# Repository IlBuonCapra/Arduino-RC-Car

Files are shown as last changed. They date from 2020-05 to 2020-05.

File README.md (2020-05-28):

# Arduino - RC Car
Arduino RC Car with nRF20L01 module, controlled by Syma X5C remote controller.
I used [Symaxrx Library](https://github.com/Suxsem/symaxrx) to control the car.

## PCB

I also created my personal shield for this projects using Eagle PCB.
Everything works with 12 volts from a battery packs made of six 18650 batteries.

A L298 Dual Full Bridge Driver is used to drive motors in each directions.
L298's enables are connected to 5 volts, so the motors are always ready to work.
If you want, you can short-circuit resistors R1,R2.
Unfortunaly, the steering motor is not controlled with PWM due to the reduced number of PWM pins of Arduino, but the car steers well.

12 volts leds are used like lights and a buzzer is used like clacson.

For this shield, i used the following pins:
| PIN | Function |
| --- | --- |
| 3 | CLACSON |
| 4 | LIGHTS |
| 5 | MOTOR1 |
| 6 | MOTOR2 |
| 7 | STEERING1 |
| 8 | STEERING2 |
| 9 | NRF_CE |
| 10 | NRF_CSN |
| 11 | NRF_MOSI |
| 12 | NRF_MISO |
| 13 | NRF_SCK |

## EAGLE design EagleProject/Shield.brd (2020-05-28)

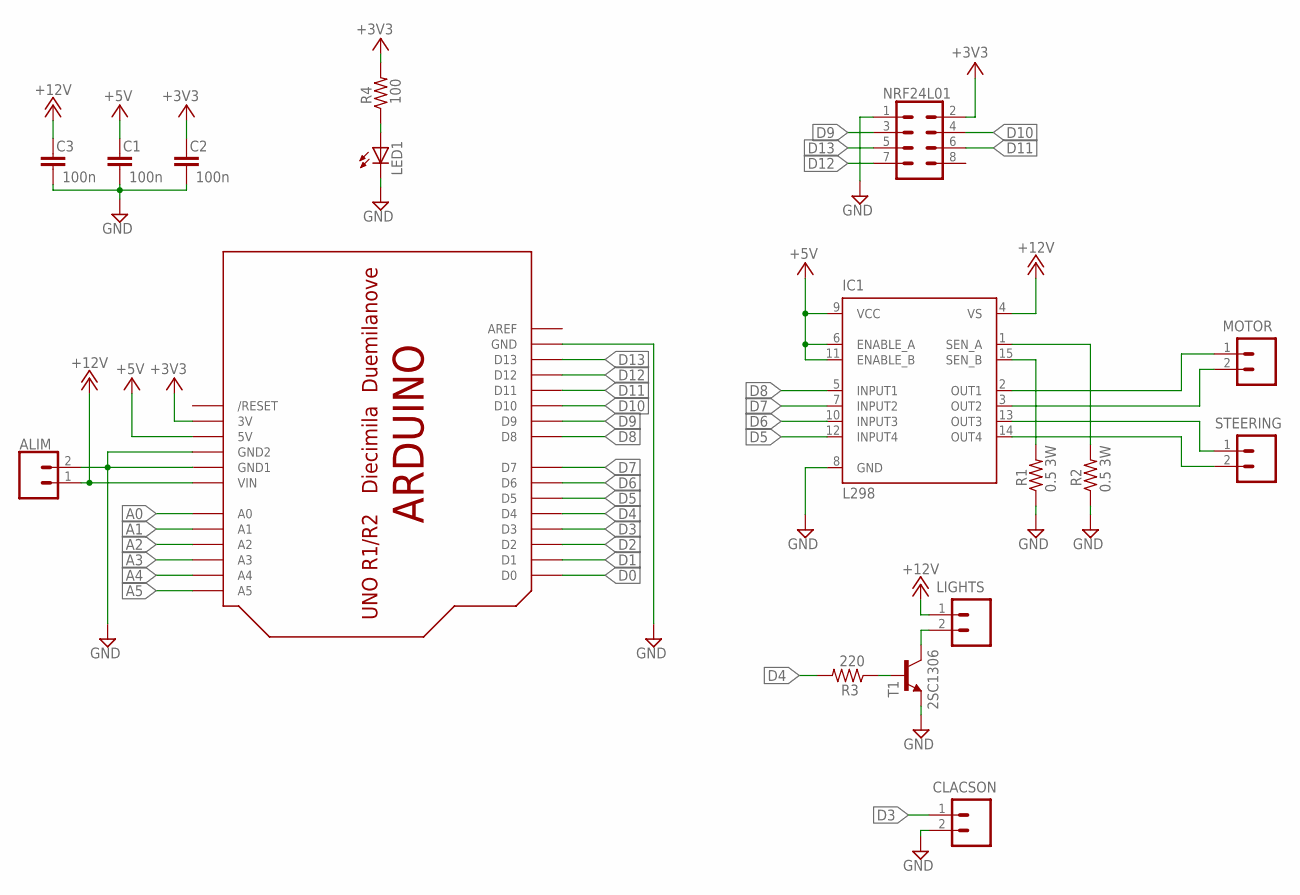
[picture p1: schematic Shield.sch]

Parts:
ALIM: CONN_025MM; SCREWTERMINAL-5MM-2
C1, C2, C3: 100n; C5B2.5
CLACSON: CONN_025MM; SCREWTERMINAL-5MM-2
IC1: L298; MULTIWATT-15
LED1: LED5MM
LIGHTS: CONN_025MM; SCREWTERMINAL-5MM-2
MOTOR: CONN_025MM; SCREWTERMINAL-5MM-2
NRF24L01: CONN_04X2; 2X4
R1, R2: 0.5 3W; 0309/12
R3: 220; 0309/12
R4: 100; 0309/12
STEERING: CONN_025MM; SCREWTERMINAL-5MM-2
T1: 2SC1306; TO220BV
U$1: ARDUINO-NOHOLE

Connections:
+3V3: C2.1, NRF24L01.2, R4.2, U$1.3V
+5V: C1.1, IC1.6 (ENABLE_A), IC1.9 (VCC), IC1.11 (ENABLE_B), U$1.5V
+12V: ALIM.1, C3.1, IC1.4 (VS), LIGHTS.1, U$1.VIN
A0: U$1.A0
A1: U$1.A1
A2: U$1.A2
A3: U$1.A3
A4: U$1.A4
A5: U$1.A5
BASE: R3.1, T1.1 (B)
COL: LIGHTS.2, T1.2 (C)
D0: U$1.D0
D1: U$1.D1
D2: U$1.D2
D3: CLACSON.1, U$1.D3
D4: R3.2, U$1.D4
D5: IC1.12 (INPUT4), U$1.D5
D6: IC1.10 (INPUT3), U$1.D6
D7: IC1.7 (INPUT2), U$1.D7
D8: IC1.5 (INPUT1), U$1.D8
D9: NRF24L01.3, U$1.D9
D10: NRF24L01.4, U$1.D10
D11: NRF24L01.6, U$1.D11
D12: NRF24L01.7, U$1.D12
D13: NRF24L01.5, U$1.D13
GND: ALIM.2, C1.2, C2.2, C3.2, CLACSON.2, IC1.8 (GND), LED1.K (C), NRF24L01.1, R1.1, R2.1, T1.3 (E), U$1.GND, U$1.GND1, U$1.GND2
unnamed: IC1.15 (SEN_B), R1.2
unnamed: LED1.A, R4.1
unnamed: IC1.3 (OUT2), MOTOR.2
unnamed: IC1.2 (OUT1), MOTOR.1
unnamed: IC1.13 (OUT3), STEERING.1
unnamed: IC1.14 (OUT4), STEERING.2
unnamed: IC1.1 (SEN_A), R2.2

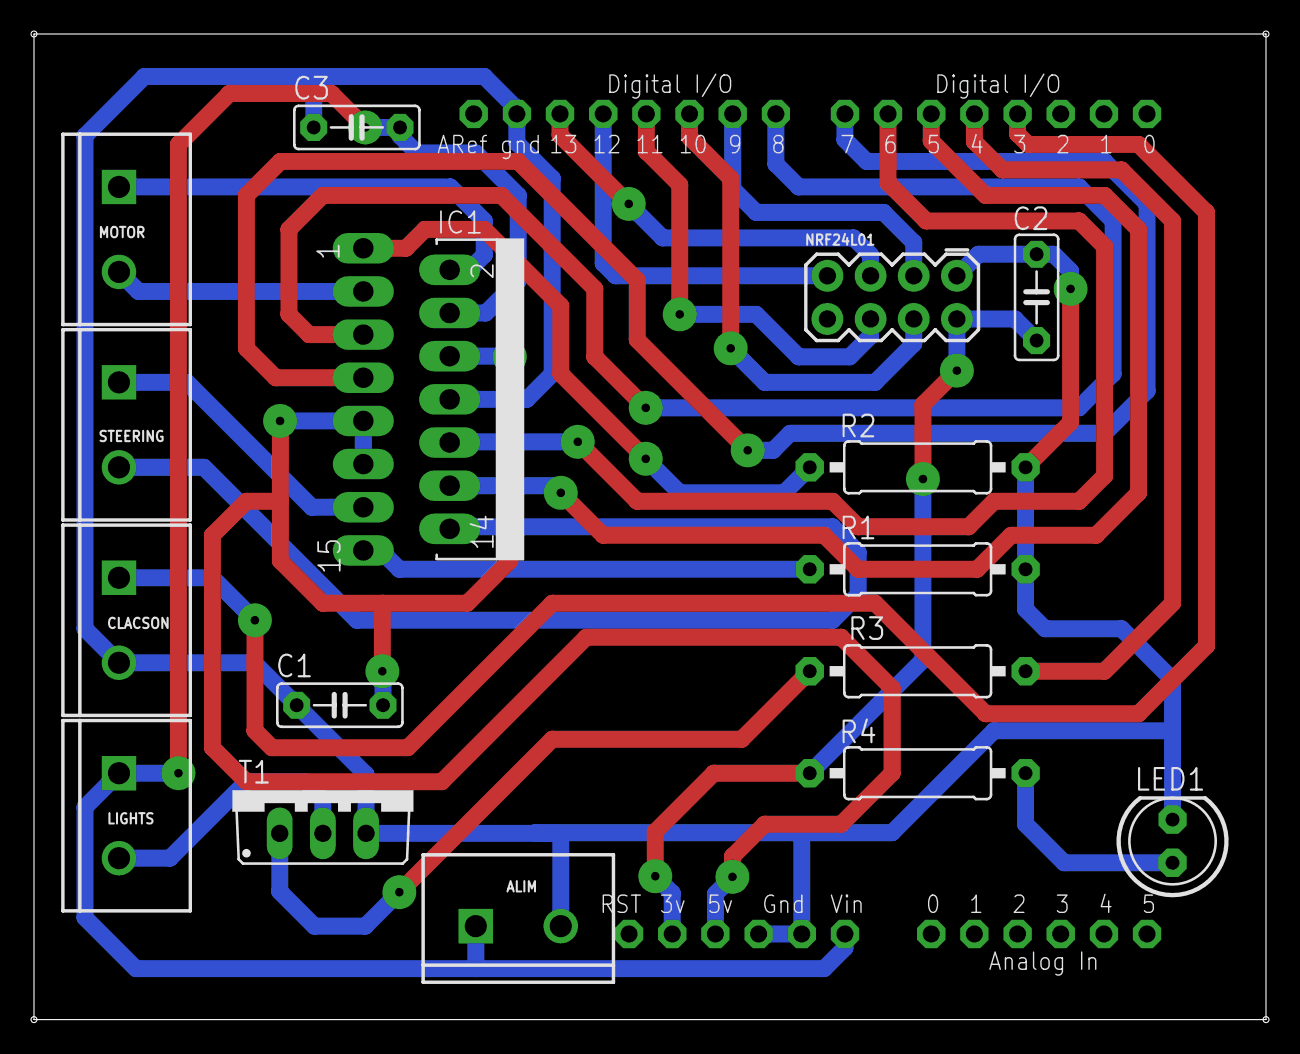
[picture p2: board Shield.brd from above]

Board: 2 copper layers, 72.5 x 58.0 mm, 17 parts (0 on the bottom side), 24 nets.

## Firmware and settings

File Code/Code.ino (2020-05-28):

#include <SPI.h>
#include <symax_protocol.h>

#define CLACSON 3
#define LIGHTS 4
#define MOTOR1 5
#define MOTOR2 6
#define STEERING1 7
#define STEERING2 8
#define NRF_CE 9
#define NRF_CS 10

nrf24l01p wireless; 
symaxProtocol protocol;
rx_values_t rxValues;
uint8_t value;

bool lostConnection = true;
bool newConnection = false;

void warning(int timer){
  digitalWrite(LIGHTS,HIGH);
  tone(CLACSON,350);
  delay(timer);
  digitalWrite(LIGHTS,LOW);
  noTone(CLACSON);
  delay(timer);
}

void setup(){
  warning(200);
  
  //Open Serial Comunication
  Serial.begin(115200);
  
  //nRF24L01
  pinMode(SS, OUTPUT);
  wireless.setPins(NRF_CE,NRF_CS);
  wireless.setPwr(PWRLOW);
  protocol.init(&wireless);
  
  //Car Output pin
  pinMode(CLACSON,OUTPUT);
  pinMode(LIGHTS,OUTPUT);
  pinMode(MOTOR1,OUTPUT);
  pinMode(MOTOR2,OUTPUT);
  pinMode(STEERING1,OUTPUT);
  pinMode(STEERING2,OUTPUT);
}

void loop(){
  value = protocol.run(&rxValues);
  switch(value){
    case  NOT_BOUND:
      if(not lostConnection){
        warning(500);
        lostConnection = true;
      }
      Serial.println("Not bound");
      analogWrite(MOTOR1,0);
      analogWrite(MOTOR2,0);
      digitalWrite(STEERING1,LOW);
      digitalWrite(STEERING2,LOW);
      newConnection = false;
      break;

    case  BIND_IN_PROGRESS:
      digitalWrite(LIGHTS,HIGH);
      Serial.println("Bind in progress");
      analogWrite(MOTOR1,0);
      analogWrite(MOTOR2,0);
      digitalWrite(STEERING1,LOW);
      digitalWrite(STEERING2,LOW);
      break;
    
    case BOUND_NEW_VALUES:
      if(not newConnection){
        digitalWrite(LIGHTS,LOW);
        warning(100);
        warning(100);
        newConnection = true;
        lostConnection = false;
      }
      
      //STEERING
      if(rxValues.roll < 40 && rxValues.roll > -40){
        digitalWrite(STEERING1,LOW);
        digitalWrite(STEERING2,LOW);
      }
      else if(rxValues.roll > 40){  //RIGHT
        digitalWrite(STEERING1,HIGH);
        digitalWrite(STEERING2,LOW);
      }
      else if(rxValues.roll < -40){ //LEFT
        digitalWrite(STEERING1,LOW);
        digitalWrite(STEERING2,HIGH);
      }
      
      //MOTOR
      if(rxValues.pitch < 40 && rxValues.pitch > -40){
        analogWrite(MOTOR1,LOW);
        analogWrite(MOTOR2,LOW);
      }
      else if(rxValues.pitch > 40 && rxValues.throttle > 75){ //FARWARD
        analogWrite(MOTOR1,LOW);
        analogWrite(MOTOR2,rxValues.throttle);
      }
      else if(rxValues.pitch < -40 && rxValues.throttle > 75){//BACK
        analogWrite(MOTOR1,rxValues.throttle);
        analogWrite(MOTOR2,LOW);
      }

      //LIGHTS
      if(rxValues.highspeed){
        digitalWrite(LIGHTS,HIGH);
      }
      else{
        digitalWrite(LIGHTS,LOW);
      }
      
      //CLACSON
      if(rxValues.flip){
        tone(CLACSON,700);
      }
      else{
        noTone(CLACSON);
      }
      
      Serial.print("\t"); Serial.print(rxValues.throttle);
      Serial.print("\t"); Serial.print(rxValues.yaw);
      Serial.print("\t"); Serial.print(rxValues.pitch);
      Serial.print("\t"); Serial.print(rxValues.roll);
      Serial.print("\t"); Serial.print(rxValues.highspeed);
      Serial.print("\t"); Serial.println(rxValues.flip);
      break;

    case BOUND_NO_VALUES:
      break;

    default:
      break;
  }
}

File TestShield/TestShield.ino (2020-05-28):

#define CLACSON 3
#define LIGHTS 4
#define MOTOR1 5
#define MOTOR2 6
#define STEERING1 7
#define STEERING2 8

void warning(int timer){
  digitalWrite(LIGHTS,HIGH);
  tone(CLACSON,350);
  delay(timer);
  digitalWrite(LIGHTS,LOW);
  noTone(CLACSON);
  delay(timer);
}

void setup() {
  //Open Serial Comunication
  Serial.begin(115200);
  
  //Car Output pin
  pinMode(CLACSON,OUTPUT);
  pinMode(LIGHTS,OUTPUT);
  pinMode(MOTOR1,OUTPUT);
  pinMode(MOTOR2,OUTPUT);
  pinMode(STEERING1,OUTPUT);
  pinMode(STEERING2,OUTPUT);

  warning(200);
}

void loop(){
  //TEST LIGHTS
  Serial.println("LIGHTS: ON");
  digitalWrite(LIGHTS,HIGH);
  delay(500);
  Serial.println("LIGHTS: OFF");
  digitalWrite(LIGHTS,LOW);
  delay(500);

  //TEST CLACSON
  Serial.println("CLACSON: ON");
  tone(CLACSON,700);
  delay(500);
  Serial.println("CLACSON: OFF");
  noTone(CLACSON);
  delay(500);

  //TEST MOTOR
  Serial.println("MOTOR1: OFF");
  Serial.println("MOTOR2: ON");
  for(int i=0; i<=255; i+=5){
    analogWrite(MOTOR1,LOW);
    analogWrite(MOTOR2,i);
    delay(100);
  }
  Serial.println("MOTOR1: OFF");
  Serial.println("MOTOR2: OFF");
  analogWrite(MOTOR1,LOW);
  analogWrite(MOTOR2,LOW);
  delay(500);

  Serial.println("MOTOR1: ON");
  Serial.println("MOTOR2: OFF");
  for(int i=0; i<=255; i+=5){
    analogWrite(MOTOR1,i);
    analogWrite(MOTOR2,LOW);
    delay(100);
  }
  Serial.println("MOTOR1: OFF");
  Serial.println("MOTOR2: OFF");
  analogWrite(MOTOR1,LOW);
  analogWrite(MOTOR2,LOW);
  delay(500);

  //TEST STEERING MOTOR
  Serial.println("STEERING1: ON");
  Serial.println("STEERING2: OFF");
  digitalWrite(STEERING1,HIGH);
  digitalWrite(STEERING2,LOW);
  delay(500);
  Serial.println("STEERING1: OFF");
  Serial.println("STEERING2: OFF");
  digitalWrite(STEERING1,LOW);
  digitalWrite(STEERING2,LOW);
  delay(500);

  Serial.println("STEERING1: OFF");
  Serial.println("STEERING2: ON");
  digitalWrite(STEERING1,LOW);
  digitalWrite(STEERING2,HIGH);
  delay(500);
  Serial.println("STEERING1: OFF");
  Serial.println("STEERING2: OFF");
  digitalWrite(STEERING1,LOW);
  digitalWrite(STEERING2,LOW);
  delay(500);
}

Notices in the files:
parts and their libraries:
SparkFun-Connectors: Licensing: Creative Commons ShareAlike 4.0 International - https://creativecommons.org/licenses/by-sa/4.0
